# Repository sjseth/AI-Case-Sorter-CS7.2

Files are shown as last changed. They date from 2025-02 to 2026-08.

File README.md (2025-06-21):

# Welcome to the CS7.2 Case Sorter Project

This project is an adaptation and upgrade of the [CS7.1 Case Sorter](https://github.com/sjseth/AI-Case-Sorter-CS7.1) project and features a number of improvements as well as a dedicated electronics package. It doesn't replace the CS7.1 solution which will still be available for the foreseeable solution but instead provides an easier route to building the AI Case Sorter for those who don't want to mess around with all the wiring and soldering required in CS7.1. 

## Getting Started

### Step 1. Choose your parts option:

If you are interested in building this project, there are two main options you can choose from. 

<font style="color:gold">**Option #1:**</font> Buy the full build kit which includes all the non-3d printed parts needed for the assembly. Choose this option if you are starting from scratch and only want to build one machine. This will usually be the cheapest option in this case. The complete build kit is available here: [CS7.2 Complete Build Kit](https://shop.sjseth.com/products/cs7-2-complete-build-kit).  **Note you will still need to provide your own 12v 5amp powersupply and a computer to run the software.* 

<font style="color:gold">**Option #2:** </font>Buy the essentials kit which includes only those parts which can be sourced from SJSeth Solutions. If you choose this route, you will need to referr to the [CS7.2 Parts List](https://www.reloadingrecipes.com/Partslist/Display/1) and acquire all the parts necessary for the build. The essentials kit can be purchase here: [CS7.2 Essentials Kit](https://shop.sjseth.com/products/cs7-2-essentials-kit)

### Step 2. Print the parts needed for your build:

This repo contains all the stl files needed to complete your build. Those files are organized by assembly and available in the [Models](./Models/) folder. For your convenience these "EZ Build" zip files have been created which have only the models which are needed/required for this project. This is to say, you just need to print everything in the zip. Refer to the assembly guides for the recommended filaments and print settings. 

* [EZ Build For Complete Build Kit](./Full%20Parts%20Kit%20Build.zip)
* [EZ Build for Essentials Kit](./Essentials%20Build.zip)

### Step 3. Assemble The Sorter

Refer to the instructions in the [Instructions Folder](./instructions/) for each of the assemblies.

* [Camera](./Instructions/CS7.2%20Camera%20Assembly%20Guide.pdf) (not needed if buying full kit)
* [Homing Sensor](./Instructions/CS7.2%20Homing%20Sensor%20Assembly%20Guide.pdf) (not needed if buying full kit)
* [Classifier](./Instructions/CS7.2%20Classifier%20Assembly%20Guide.pdf)
* [Sorter](./Instructions/CS7.2%20Sorter%20Assembly%20Guide.pdf)
* [Electronics Enclosure](./Instructions/CS7.2%20Electronics%20Box%20Assembly.pdf)

### Step 4. Install the software and read the manual
You need to register for an account to download the software. You can do this at [https://www.reloadingrecipes.com/HeadstampSorter](https://www.reloadingrecipes.com/HeadstampSorter). 

Here is the link to the latest software manual: [AI Headstamp Sorter Application Guide for v1.1.53](./Instructions/AI%20Headstamp%20Sorter%20Application%20Guide_11531.pdf)

## CS7.2 Build Series Videos
### Camera Assembly
Camera Assembly (https://youtu.be/B2Un%2Dj%2DgyE4)

### Homing Sensor Assembly
Homing Sensor (https://youtu.be/8RCl6ofWERs)

### Classifier Assembly
Classifier Assembly (https://youtu.be/V4ZLb2sHJYE)

### Sorter Assembly
Sorter Assembly (https://youtu.be/yfZtguaGFcg)

### Electronics Box Assembly
Electroncis Box (https://youtu.be/7Ex8II1yqZ4)

### Final Assembly - putting it all together. 
Putting it all together (https://youtu.be/NzxutLAYxv8)

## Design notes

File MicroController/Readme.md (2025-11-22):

# CS7.2 Firmware

## Installing the firmware
1. Install Arduino Studio (https://www.arduino.cc/en/software/)
2. Download the latest firmware zip file from this folder (https://github.com/sjseth/AI-Case-Sorter-CS7.2/tree/main/MicroController)
3. Extract the zipfile and navigate into the folder and double-click on the CS72_Firmware.ino file to launch the file in the studio
4. In Arduino Studio, open the library panel (the icon on the left side which looks like books) and search for TMCStepper
5. Install the TMCStepper Library
6. Identify which COM port your board is plugged into. YOu can turn off the board and check the list of ports, then turn it back on. The new one that appears will be the com port for your board
7. Select the board/com port and set the board type as Arduino Uno
8. Push/Upload the firmware to the boards.  This is the button in the top left of the studio which looks like an arrow.

# Video Instructions

Updating Firmware On Board (https://youtu.be/qdWw8pG_hVo)

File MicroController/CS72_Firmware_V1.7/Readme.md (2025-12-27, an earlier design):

# V1.7 Firmware

## Important! This firmware is for v1.7 boards and newer. Right now, all the v1.7 boards are yellow... If your board isn't yellow, this won't work for you!

The board versions can be found in the lower left corner of the PCB. 

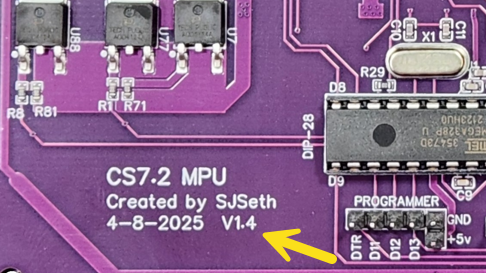
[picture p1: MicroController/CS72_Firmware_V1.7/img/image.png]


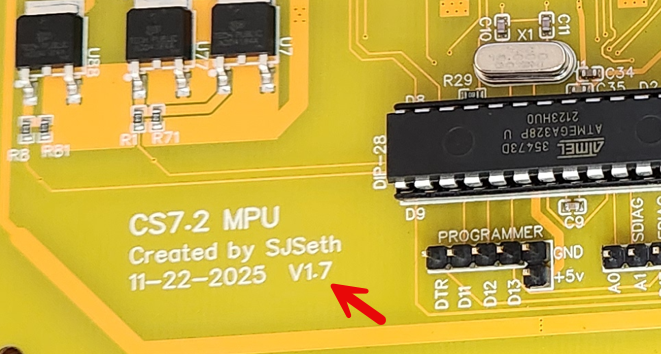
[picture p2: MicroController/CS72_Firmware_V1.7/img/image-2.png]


# FAQ

Q: What can this firmware do that the previous versions can't?

A: The v1.7+ boards have the TMC2209 diag pins wired up so that we can use the stallguard feature which allows us to monitor the current/resistance on the motor to detect a stall/jam.

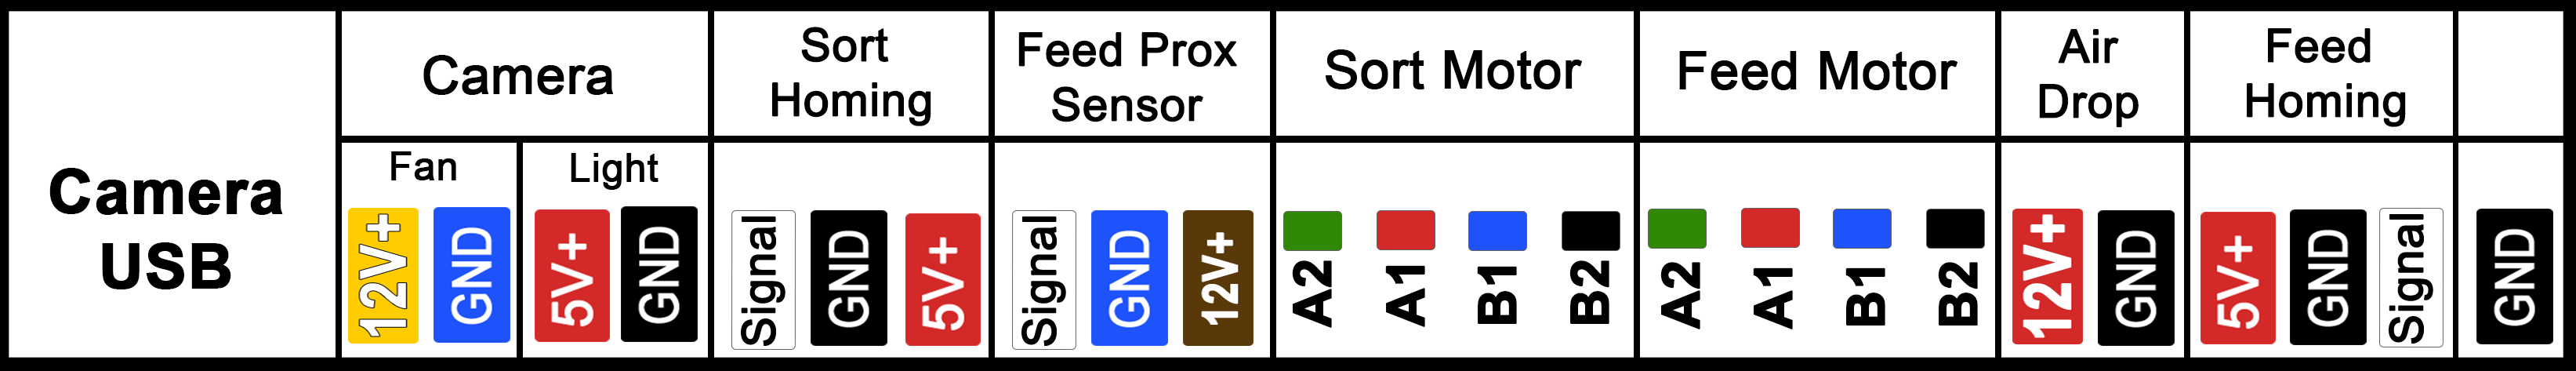
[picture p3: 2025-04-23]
Models/Electronics Enclosure/box_label_v3.png

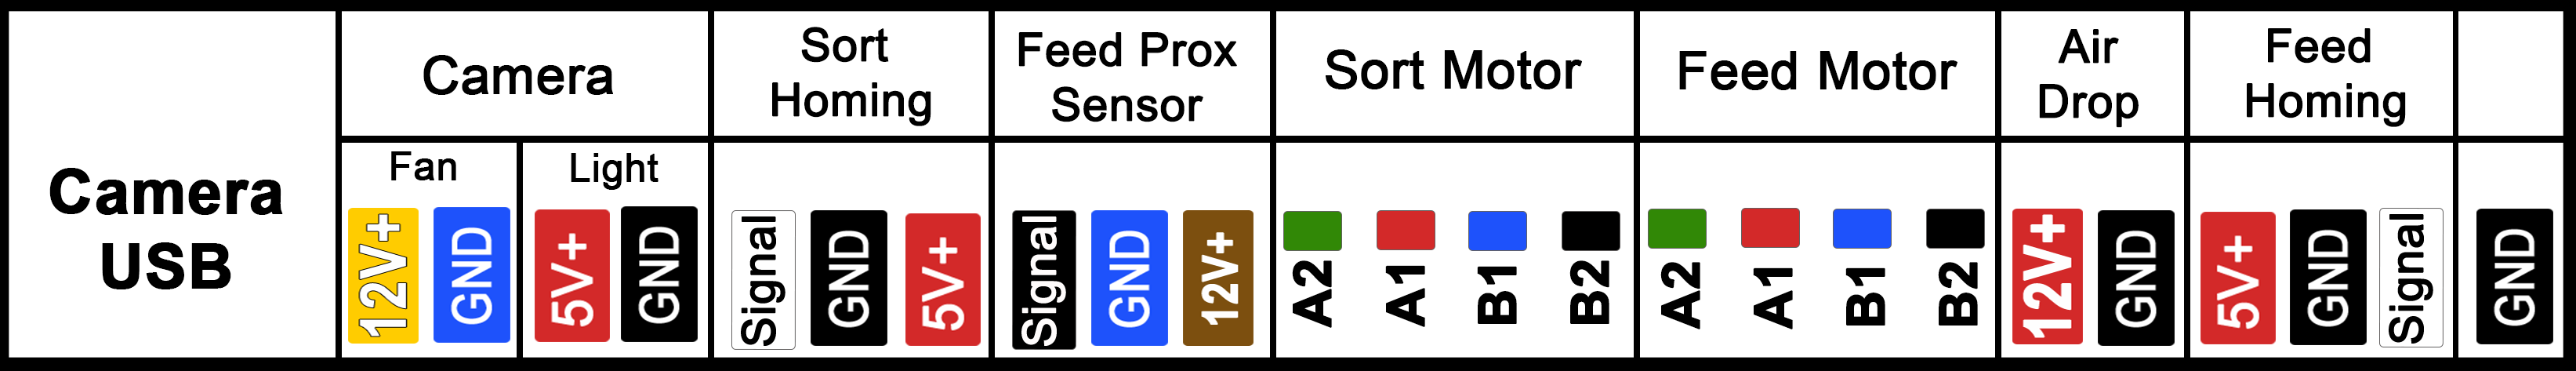
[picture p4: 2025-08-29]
Models/Electronics Enclosure/box_label_new.png

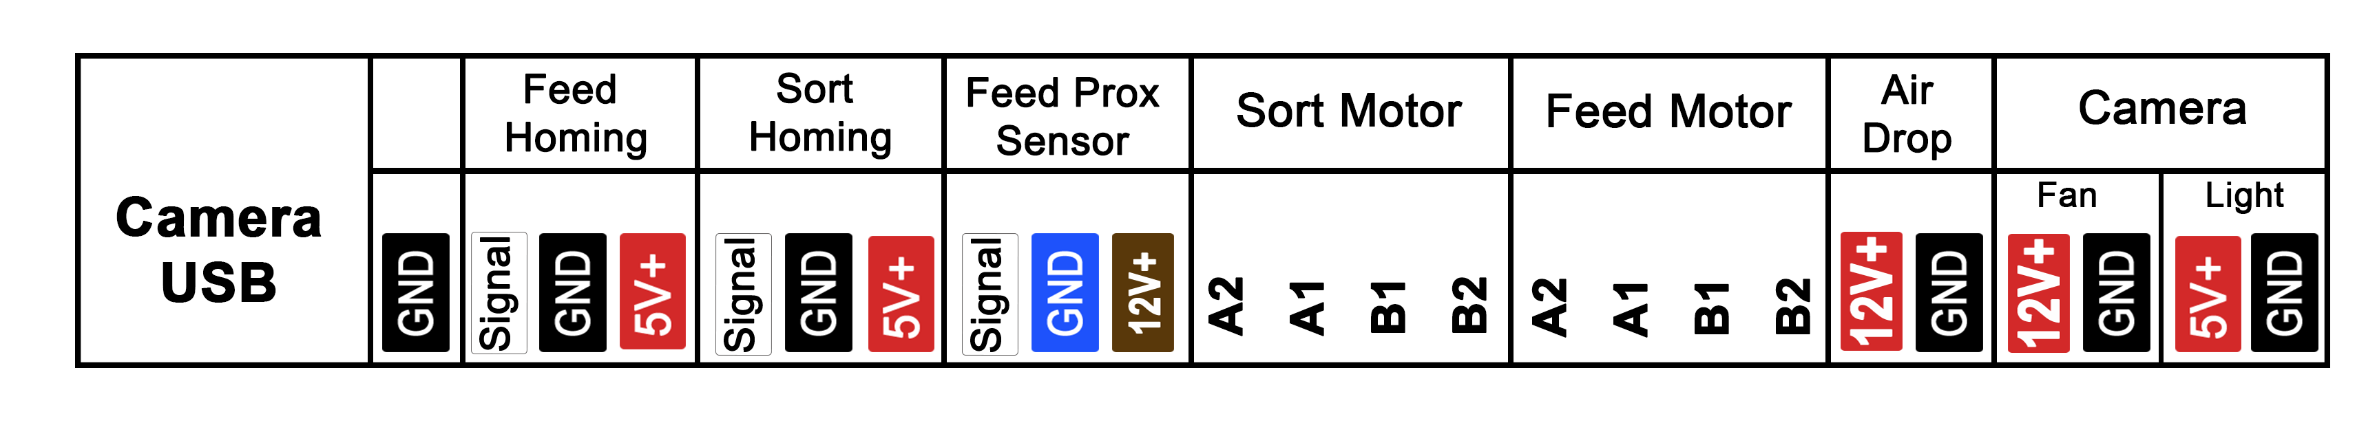
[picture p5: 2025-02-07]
Models/Electronics Enclosure/v1-v2/box_label_V2.png

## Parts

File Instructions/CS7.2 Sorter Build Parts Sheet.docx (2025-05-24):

(5) M3x8 Socket Head Cap Screw (2) Homing Sensor (1) Bracket Lock (2) Sort Pipe Set Screws | (4) M3x14 Phillips Pan Head Screw Motor Mount | (4) M3 Washers Motor Mount | (4) M3x12 Phillips Pan Head Screw Flange Motor Mount Screws
(1) 5mm Motor Flange with lock screws Motor Flange Coupler | (1) M3x18 Socket Head Cap Screws Homing Interrupter

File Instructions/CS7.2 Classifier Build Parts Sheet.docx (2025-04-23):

(1) M8x1.0 Heat Set Insert (for proximity sensor) Proximity Sensor | (1) M6x80 Socket Head Cap Screw Main Axle | (3) M6x30 Socket Head Cap Screws (1) Tension Cam Axle (2) Mount Screws | (1) M3x18 Socket Head Cap Screw Tension Cam Spring Mount
(1) M4x8 Socket Head Cap Screw Tension Cam Stop | (4) M3x12 Socket Head Cap Screws Motor Mount Screws | (2) M3x16 Socket Head Cap Screws Camera and Drop Tube Set Screws | (1) 5x5x30 Stainless Steel Tension Spring Tension Cam Spring
(1) M3 Nut (tension cam mount lock) Spring Mount Nut | (1) 5mm Motor Flange with lock screws Motor Flange Coupler | (4) M3x12 Phillips Pan Head Flange Gear Mount Screws | (2) 626zz Bearings Feed Wheel Bearings
(3) M3x8 Socket Head Cap Screws (2) Homing Sensor Mount (1) Light Shade Set Screw | (1) M3 Heat Set Insert Light Shade Lock | (1) .3x4x20mm Compression Spring Homing Sensor

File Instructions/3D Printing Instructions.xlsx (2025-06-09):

Part | Assembly | Quantity Required | Included in Full Kit | Filament Color | Recommended Filament Type | Layer Height | Infill | Walls | Support Type | Support Angle | Raft Layers | Github URL
Caliber Feed Wheels(all) | Classifier | 1 | No | Black | PLA+, PETG | 0.2 | 25 | 3 | organic tree | 3 | 0 | https://github.com/sjseth/AI-Case-Sorter-CS7.2/tree/main/Models/CaliberFeedSets/
CS7.2 Camera Housing.stl | Camera | 1 | Yes | Black | PLA+, PETG | 0.16 | 15 | 2 | none |  | 0 | https://github.com/sjseth/AI-Case-Sorter-CS7.2/tree/main/Models/Camera/CS7.2 Camera Housing.stl
CS7.2 Camera Light Diffuser.stl | Camera | 1 | Yes | White (non opaque) | PLA, PLA+ | 0.16 | 0 | 2 | none |  | 0 | https://github.com/sjseth/AI-Case-Sorter-CS7.2/tree/main/Models/Camera/CS7.2 Camera Light Diffuser.stl
CS72 - Camera Focus Jig.stl | Camera | 1 | No | Black | PLA+, PETG | 0.2 | 20 | 3 | none |  | 0 | https://github.com/sjseth/AI-Case-Sorter-CS7.2/tree/main/Models/Camera/CS72 - Camera Focus Jig.stl
CS7.2 Classifier Base.stl | Classifier | 1 | No | Black | PLA+, PETG | 0.2 | 20 | 3 | none |  | 0 | https://github.com/sjseth/AI-Case-Sorter-CS7.2/tree/main/Models/Classifier/CS7.2 Classifier Base.stl
CS7.2 Classifier Drop Nozzle.stl | Classifier | 1 | No | Any | PLA+, PETG | 0.2 | 20 | 3 | organic tree | 3 | 0 | https://github.com/sjseth/AI-Case-Sorter-CS7.2/tree/main/Models/Classifier/CS7.2 Classifier Drop Nozzle.stl
CS7.2 Drive Gear.stl | Classifier | 1 | No | Any | PLA+, PETG | 0.2 | 20 | 3 | none |  | 0 | https://github.com/sjseth/AI-Case-Sorter-CS7.2/tree/main/Models/Classifier/CS7.2 Drive Gear.stl
CS7.2 Feed Bracket.stl | Feed | 1 | No | Any | PLA+, PETG | 0.2 | 20 | 3 | organic tree | 3 | 0 | https://github.com/sjseth/AI-Case-Sorter-CS7.2/tree/main/Models/Classifier/CS7.2 Feed Bracket.stl
CS7.2 Homing Sensor.stl | Classifier | 1 | Yes | Any | PLA+, PETG | 0.16 | 20 | 3 | none |  | 0 | https://github.com/sjseth/AI-Case-Sorter-CS7.2/tree/main/Models/Classifier/CS7.2 Homing Sensor.stl
CS7.2 Tension Cam Shim.stl | Classifier | 1 | No | Any | PLA+, PETG | 0.2 | 20 | 3 | none |  | 1 | https://github.com/sjseth/AI-Case-Sorter-CS7.2/tree/main/Models/Classifier/CS7.2 Tension Cam Shim.stl
CS7.2 Tension Cam.stl | Classifier | 1 | No | Any | PLA+, PETG | 0.2 | 20 | 3 | tree | 3 | 0 | https://github.com/sjseth/AI-Case-Sorter-CS7.2/tree/main/Models/Classifier/CS7.2 Tension Cam.stl
CS7.2 Wheel Lock - Light Shade.stl | Classifier | 1 | No | Any | PLA+ | 0.2 | 20 | 3 | none |  | 0 | https://github.com/sjseth/AI-Case-Sorter-CS7.2/tree/main/Models/Classifier/CS7.2 Wheel Lock - Light Shade.stl
CS7.2 Electronics Box Lid.stl | Electronics Enclosure | 1 | No | Any | PLA+ | 0.2 | 20 | 3 | none |  | 0 | https://github.com/sjseth/AI-Case-Sorter-CS7.2/tree/main/Models/Electronics Enclosure/CS7.2 Electronics Box Lid.stl
CS7.2 Electronics Box.stl | Electronics Enclosure | 1 | No | Any | PLA+ | 0.2 | 20 | 3 | organic tree | 3 | 0 | https://github.com/sjseth/AI-Case-Sorter-CS7.2/tree/main/Models/Electronics Enclosure/CS7.2 Electronics Box.stl
CS7.2 Mount with Rotator - Plate.stl | Electronics Enclosure | 1 | No | Any | PLA+, PETG | 0.2 | 20 | 3 | none |  | 0 | https://github.com/sjseth/AI-Case-Sorter-CS7.2/tree/main/Models/Electronics Enclosure/CS7.2 Mount with Rotator - Plate.stl
CS7.2 Mount with Rotator.stl | Electronics Enclosure | 1 | No | Any | PLA+, PETG | 0.2 | 20 | 3 | none |  | 0 | https://github.com/sjseth/AI-Case-Sorter-CS7.2/tree/main/Models/Electronics Enclosure/CS7.2 Mount with Rotator.stl
CS7.2 Wire Cover.stl | Electronics Enclosure | 1 | No | Any | PLA+, PETG | 0.2 | 20 | 3 | none |  | 0 | https://github.com/sjseth/AI-Case-Sorter-CS7.2/tree/main/Models/Electronics Enclosure/CS7.2 Wire Cover.stl
CS7.2 Thumbscrew Cap.stl | Misc | (optional) 5 | No | Any | PLA+, PETG | 0.2 | 20 | 3 | none |  | 0 | https://github.com/sjseth/AI-Case-Sorter-CS7.2/tree/main/Models/Misc/CS7.2 Thumbscrew Cap.stl
CS7.2 Pole Mount - 1.050 with Channel.stl | Mounts | 3 | No | Any | PLA+, PETG | 0.2 | 25 | 3 | none |  | 0 | https://github.com/sjseth/AI-Case-Sorter-CS7.2/tree/main/Models/Mounts/CS7.2 Pole Mount - 1.050 with Channel.stl
CS7.2 Pole Mount - 1.050.stl | Mounts | (optional) 1 | No | Any | PLA+, PETG | 0.2 | 25 | 3 | none |  | 0 | https://github.com/sjseth/AI-Case-Sorter-CS7.2/tree/main/Models/Mounts/CS7.2 Pole Mount - 1.050.stl
CS7.2 Wire Mgmt Clip.stl | Mounts | (optional) 4 | No | Any | PLA+ | 0.2 | 20 | 3 | none |  | 1 | https://github.com/sjseth/AI-Case-Sorter-CS7.2/tree/main/Models/Mounts/CS7.2 Wire Mgmt Clip.stl
CS7.2 Pipe Bracket.stl | Sorter | 1 | No | Any | PLA+, PETG | 0.2 | 20 | 3 | none |  | 0 | https://github.com/sjseth/AI-Case-Sorter-CS7.2/tree/main/Models/Sorter/CS7.2 Pipe Bracket.stl
CS7.2 Sort Pipe - 40mm LO.stl | Sorter | 1 | No | Any | PLA+, PETG | 0.2 | 15 | 2 | none |  | 0 | https://github.com/sjseth/AI-Case-Sorter-CS7.2/tree/main/Models/Sorter/CS7.2 Sort Pipe - 40mm LO.stl
CS7.2 Sorter Base.stl | Sorter | 1 | No | Any | PLA+, PETG | 0.2 | 20 | 3 | none |  | 0 | https://github.com/sjseth/AI-Case-Sorter-CS7.2/tree/main/Models/Sorter/CS7.2 Sorter Base.stl
CS7.2 Sorter Homing Interupt.stl | Sorter | 1 | No | Black | PLA+, PETG | 0.2 | 20 | 3 | none |  | 0 | https://github.com/sjseth/AI-Case-Sorter-CS7.2/tree/main/Models/Sorter/CS7.2 Sorter Homing Interupt.stl

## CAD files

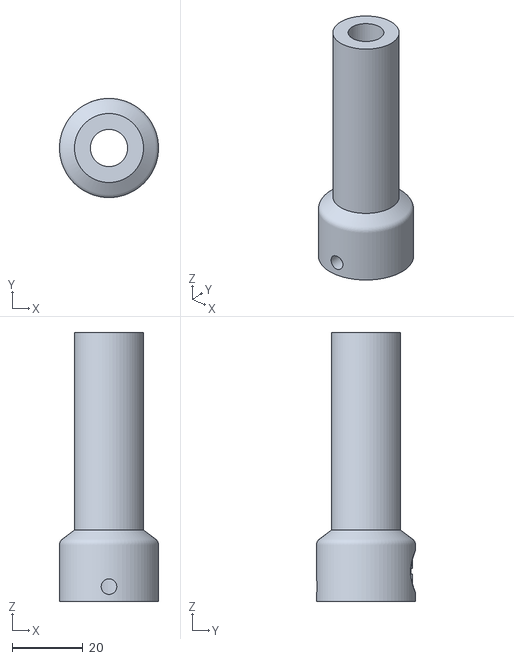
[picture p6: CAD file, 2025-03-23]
Models/CaliberFeedSets/223_556/CS7.2 Feed Tube - 223_556 (S).stl
28.0 x 28.0 x 76.0

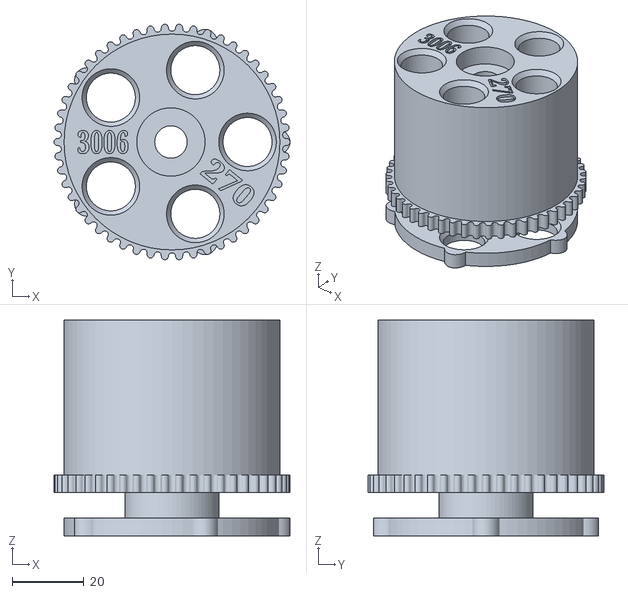
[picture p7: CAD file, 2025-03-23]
Models/CaliberFeedSets/30-06_270/CS7.2 Feed Wheel - 30.06 - (S).stl
65.6 x 65.5 x 60.0

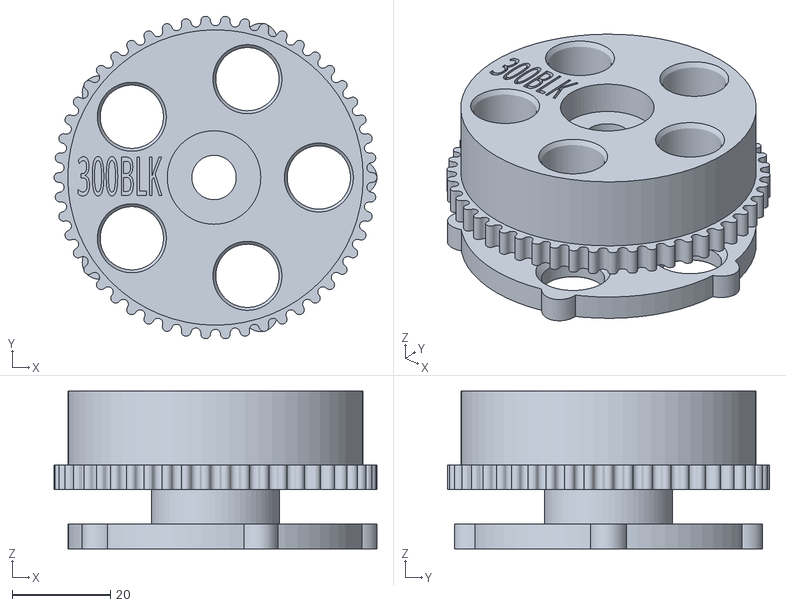
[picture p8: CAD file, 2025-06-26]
Models/CaliberFeedSets/300_Blackout/CS7.2 300 Blackout Feed Wheel.stl
65.6 x 65.5 x 32.0

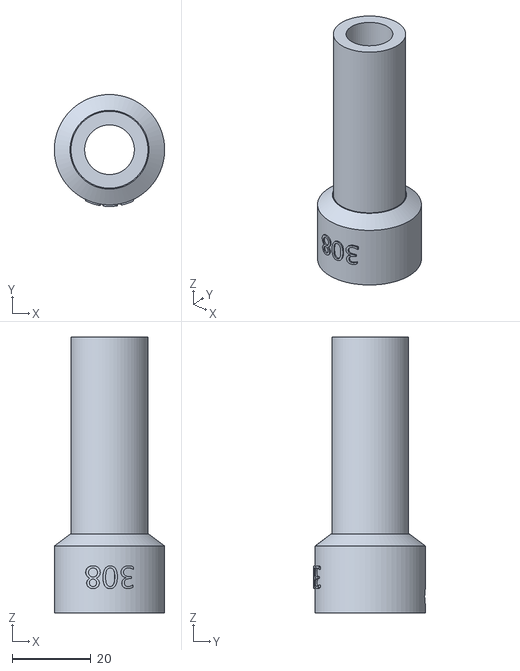
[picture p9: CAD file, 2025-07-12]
Models/CaliberFeedSets/308win/CS7.x 308Win Feed Nozzle.stl.stl
28.0 x 28.4 x 70.0

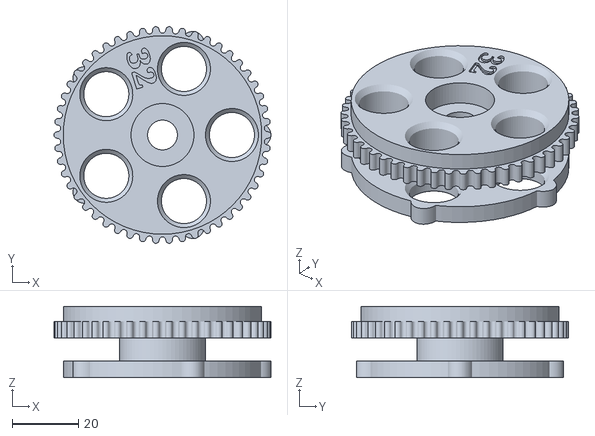
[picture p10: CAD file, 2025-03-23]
Models/CaliberFeedSets/32SWLong/CS7.2 Feed Wheel - 32SWLong - (S).stl
65.6 x 65.5 x 21.6

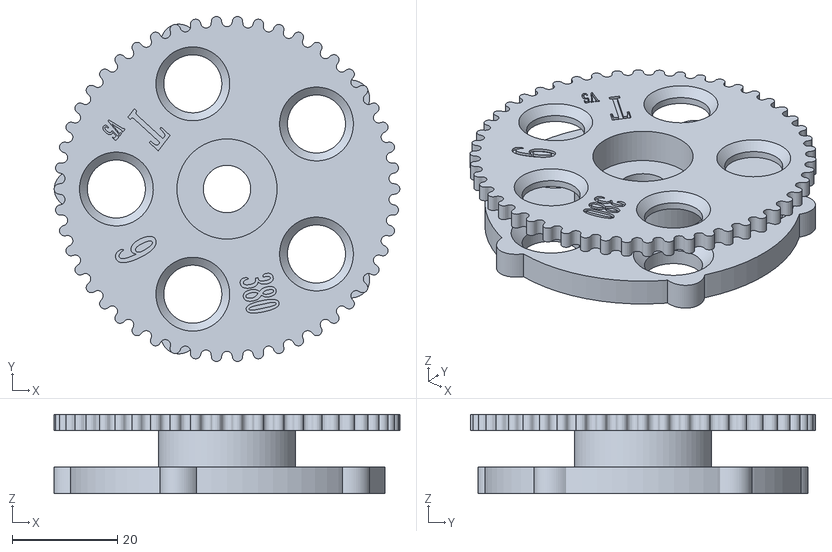
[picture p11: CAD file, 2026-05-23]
Models/CaliberFeedSets/380-9mm/CS7.x 9mm 380 Feed Wheel - Tight v5.stl
65.6 x 65.5 x 15.0

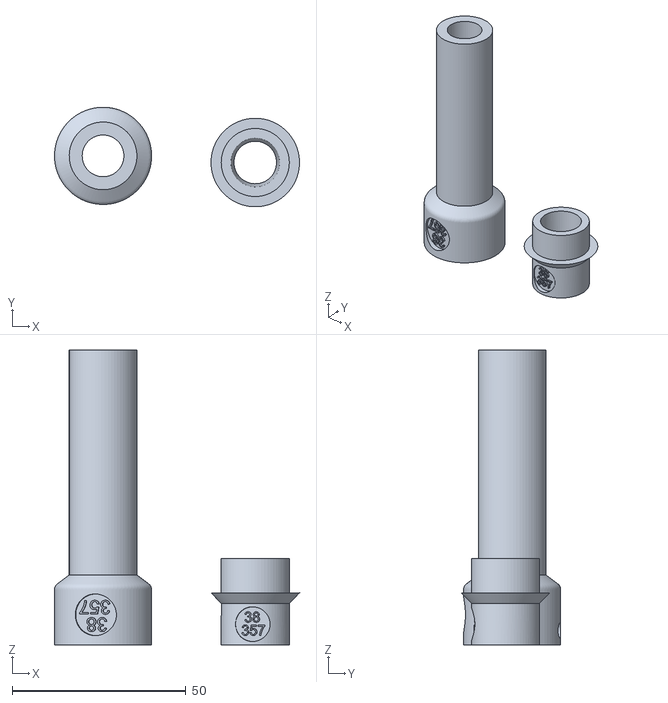
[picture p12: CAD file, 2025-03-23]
Models/CaliberFeedSets/38_Special/CS7.2 Feed Nozzle - 38Special - (S).stl
70.6 x 28.7 x 85.0

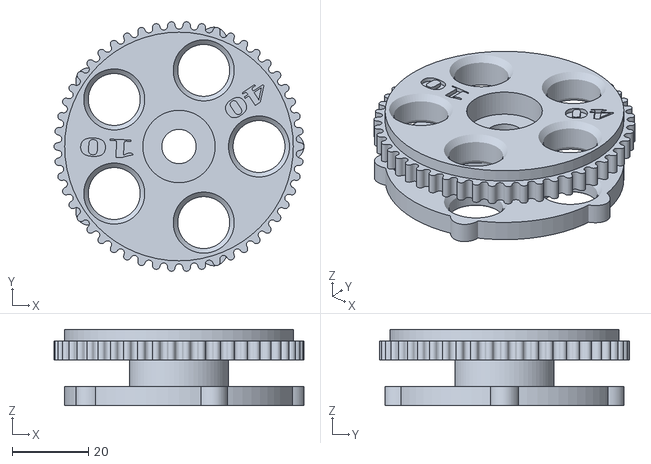
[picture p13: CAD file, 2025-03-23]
Models/CaliberFeedSets/40SW/CS7.2 Feed Wheel - 40SW (S).stl
65.6 x 65.5 x 20.0

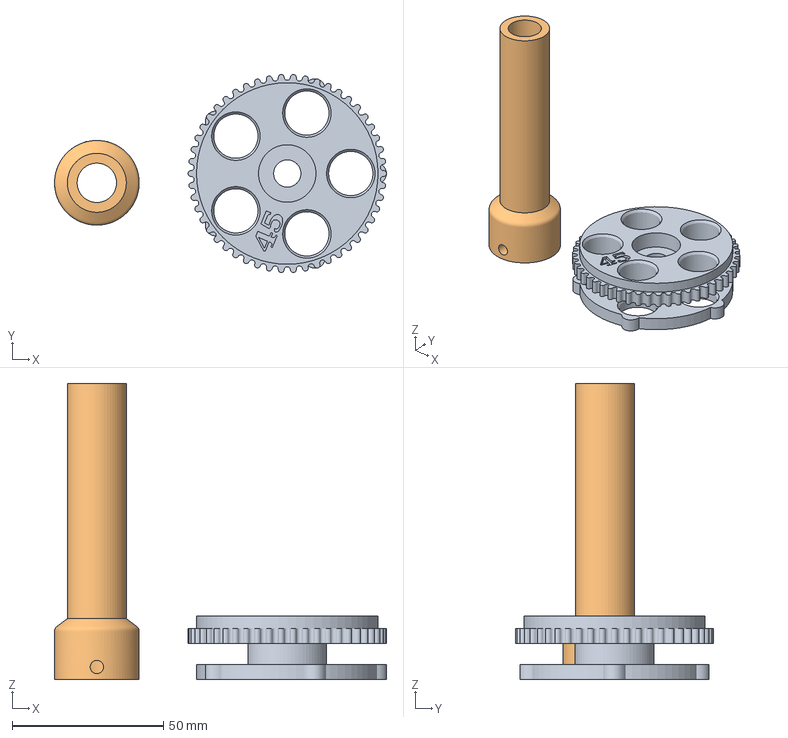
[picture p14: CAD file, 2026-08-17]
Models/CaliberFeedSets/45Auto/CS7.2 Feed Wheel 45AUTO (S).3mf
109.8 x 65.5 x 98.0 mm
CS7.2 Feed Wheel 45AUTO (S).stl
CS7.2 Feed Nozzle 45AUTO-GAP (S).stl_1

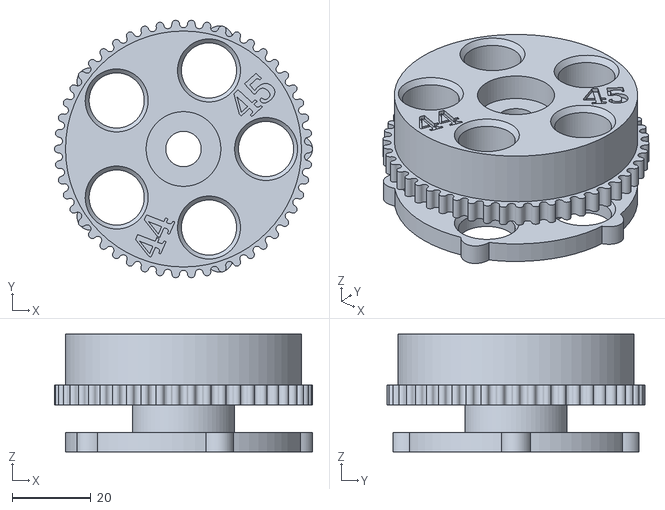
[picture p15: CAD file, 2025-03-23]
Models/CaliberFeedSets/45Colt_44Mag/CS7.2 Feed Wheel - 44MAG_45COLT (S).stl
65.6 x 65.5 x 30.0

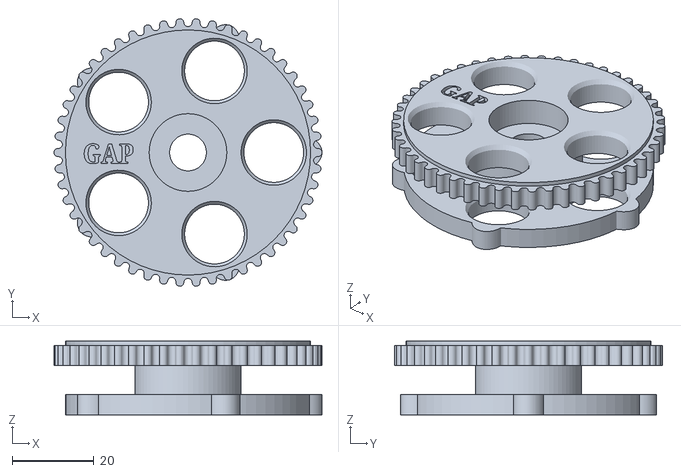
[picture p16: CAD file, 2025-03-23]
Models/CaliberFeedSets/45GAP/CS7.2 Feed Wheel - 45GAP - (S).stl
65.6 x 65.5 x 18.0

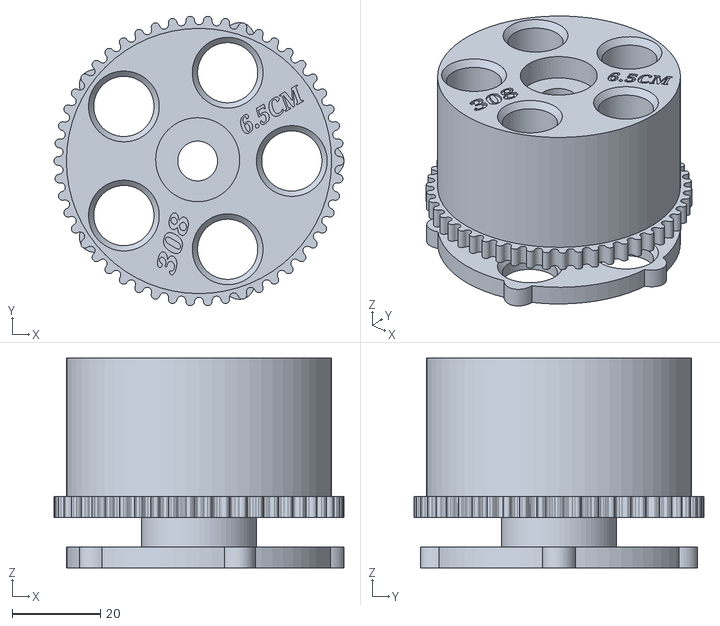
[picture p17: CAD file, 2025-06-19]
Models/CaliberFeedSets/6.5_Creedmoor/CS7.2 Feed Wheel - 6.5 Creedmoor (S).stl
65.6 x 65.5 x 47.5

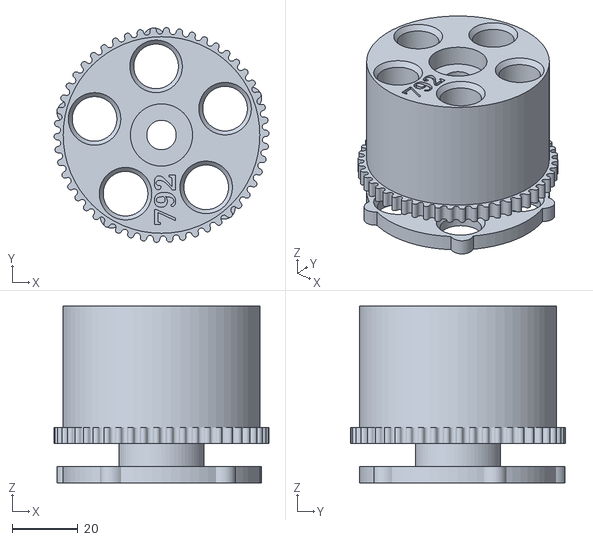
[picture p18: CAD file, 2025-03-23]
Models/CaliberFeedSets/7.92x57_Mauser/CS7.2 Feed Wheel - 7.92x57M - (S).stl
65.6 x 65.6 x 54.0

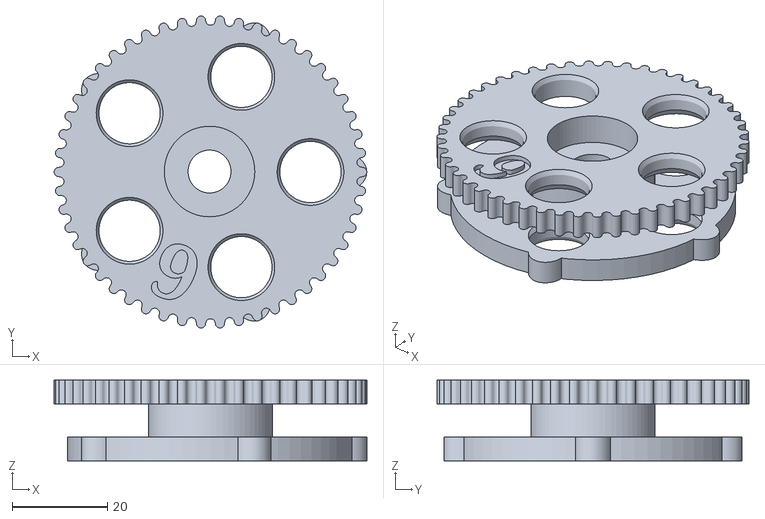
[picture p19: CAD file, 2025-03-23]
Models/CaliberFeedSets/9mm/CS7.2 Feed Wheel 9mm (S).stl
65.6 x 65.5 x 17.0

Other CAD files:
Models/CaliberFeedSets/CSxDrop_Nozzles/CS7.x 38 Special Drop Nozzle.stl
Models/CaliberFeedSets/CSxFeed_Tubes/CS7.x 30.06 Feed Tube.stl
Models/Camera/4010 Blower Fan Tuyere - Air Guide.stl
Models/Classifier/CS7.2 Homing Sensor V2.3mf
Models/CaliberFeedSets/223_556/CS7.2 Feed Tube - 223_556.stl
Models/CaliberFeedSets/223_556/CS7.2 Feed Wheel - 223_556 (S).stl
Models/CaliberFeedSets/30-06_270/CS7.2 Feed Nozzle - 30.06 - (S).stl
Models/CaliberFeedSets/300_Blackout/CS7.2 300 Blackout Feed Nozzle.stl
Models/CaliberFeedSets/308win/CS7.2 Feed Nozzle - 308 (S).stl
Models/CaliberFeedSets/308win/CS7.2 Feed Wheel - 308 (S).stl
Models/CaliberFeedSets/32SWLong/CS7.2 Feed Nozzle - 32SWLong - (S).stl
Models/CaliberFeedSets/380-9mm/CS7.2 Feed Nozzle - 9mm - 380 (S).stl
Models/CaliberFeedSets/380-9mm/CS7.2 Feed Wheel - 9mm - 380 (S).stl
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

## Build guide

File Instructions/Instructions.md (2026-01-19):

# Welcome to the CS7.2 Case Sorter Project

This project is an adaptation of the [CS7.1 Case Sorter](https://github.com/sjseth/AI-Case-Sorter-CS7.1) project and features a number of improvements as well as a dedicated electronics package. It doesn't replace the CS7.1 solution which will still be available for the foreseeable solution but instead provides an easier route to building the AI Case Sorter for those who don't want to mess around with all the wiring and soldering required in CS7.1. 

## Getting Started

### Step 1. Choose your parts option:

If you are interested in building this project, there are two main options you can choose from. 

<font style="color:gold">**Option #1:**</font> Buy the full build kit which includes all the non-3d printed parts needed for the assembly. Choose this option if you are starting from scratch and only want to build one machine. This will usually be the cheapest option in this case. The complete build kit is available here: [CS7.2 Complete Build Kit](https://shop.sjseth.com/products/cs7-2-complete-build-kit).  **Note you will still need to provide your own 12v 5amp powersupply and a computer to run the software.* 

<font style="color:gold">**Option #2:** </font>Buy the essentials kit which includes only those parts which can be sourced from SJSeth Solutions. If you choose this route, you will need to referr to the [CS7.2 Parts List](https://www.reloadingrecipes.com/Partslist/Display/1) and acquire all the parts necessary for the build. The essentials kit can be purchase here: [CS7.2 Essentials Kit](https://shop.sjseth.com/products/cs7-2-essentials-kit)

### Step 2. Print the parts needed for your build:

This repo contains all the stl files needed to complete your build. Those files are organized by assembly and available in the [Models](../Models/) folder. For your convenience these "EZ Build" zip files have been created which have only the models which are needed/required for this project. This is to say, you just need to print everything in the zip. Refer to the assembly guides for the recommended filaments and print settings. 

* [EZ Build For Complete Build Kit](../Full%20Parts%20Kit%20Build.zip)
* [EZ Build for Essentials Kit](../Essentials%20Build.zip)

#### Step 2a. Reuse parts from your CS7.1 Build:

If you have a 7.1 build, these parts are reusable in 7.2
- Light Shade
- Feed Tubes
- Feed Bracket
- Feed Wheels (caliber sets)
- Drop Tube
- Tension Cam Shim
- Drive Gear
- Sorting Bins
- Pole Mount Brackets (though the new ones have wire management channels)

### Step 3. Assemble The Sorter

Refer to the instructions in the [Instructions Folder](./instructions/) for each of the assemblies.

* [Camera](./CS7.2%20Camera%20Assembly%20Guide.pdf) (not needed if buying full kit)
* [Homing Sensor](./CS7.2%20Homing%20Sensor%20Assembly%20Guide.pdf) (not needed if buying full kit)
* [Classifier](./CS7.2%20Classifier%20Assembly%20Guide.pdf)
* [Sorter](./CS7.2%20Sorter%20Assembly%20Guide.pdf)
* [Electronics Enclosure](./CS7.2%20Electronics%20Box%20Assembly.pdf)

## CS7.2 Build Series Videos

### Camera Assembly
Camera Assembly (https://youtu.be/B2Un%2Dj%2DgyE4)

### Homing Sensor Assembly
Homing Sensor (https://youtu.be/8RCl6ofWERs)

### Classifier Assembly
Classifier Assembly (https://youtu.be/V4ZLb2sHJYE)

### Sorter Assembly
Sorter Assembly (https://youtu.be/yfZtguaGFcg)

### Electronics Box Assembly
Electroncis Box (https://youtu.be/7Ex8II1yqZ4)

### Final Assembly - putting it all together. 
Putting it all together (https://youtu.be/NzxutLAYxv8)

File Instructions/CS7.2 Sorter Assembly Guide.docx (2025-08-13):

# CS7.2 Sorter Assembly Guide

# Printing the parts

The models for the 3d printed parts for the classifier base are available in the “Sorter” folder in the GitHub CS7.2 repo.

https://github.com/sjseth/AI-Case-Sorter-CS7.2/tree/main/Models/Sorter

From this folder, you need to print the following models.

- CS7.2 Pipe Bracket
- CS7.2 Sort Pipe – 40mm LO or CS7.2 Sort Pipe – 200mm LO
- CS7.2 Sorter Base
- CS7.2 Sorter Homing Interrupt

For these parts here are the basic recommendations:

Filament: PLA+ or PETG.

Color: These parts can be printed in any color you have available.

Layer Height: .2 or finer

Support: Recommend using tree support for the sorter base, however, use the support mode you get the best results with on your printer. For Bambu printers, I have found these settings work well:

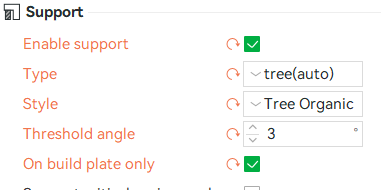
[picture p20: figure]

Note that other slices such as Cura, the support angle may read 87 degrees (opposite of Bambu/Orca slicer)

Strength/Density: 3 walls, 20% infill

# Assembly

Tools Required:

- Screwdriver with bits or Allen keys for M3, M6 socket head cap screws
- Small Phillips head screwdriver

Hardware required:

- (4) M3x14 Phillips Head Screws (motor mount)
- (4) M3 washers
- (4) M3x12 Phillips Head Screws (for flange mount)
- (3) M3x8 Socket Head Screw (set screw for base mount and sort pipe)
- (1) 5mm Motor Flange with lock screws
- (1) m3x18 Socket Head (clamp screw for homing interrupter)
- (optional) Small Zip Ties .1”W x 4”L

Electronics

- (1) Nema 17 Motor
- (1) Optical Homing Sensor

The following diagram is a quick reference to where the hardware belongs.

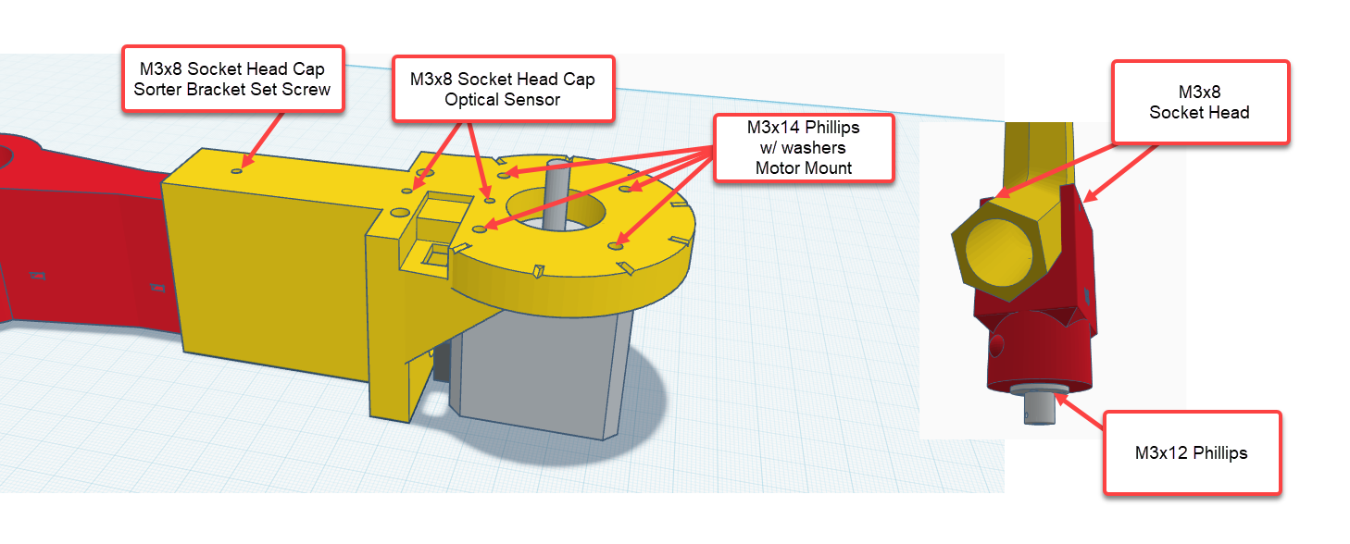
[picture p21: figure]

## Assembly Steps

1. Remove 3d printed support material from Sorter Base.
2. Run cable for sensor passing it through the inside of the sorter base, and up through the square hole

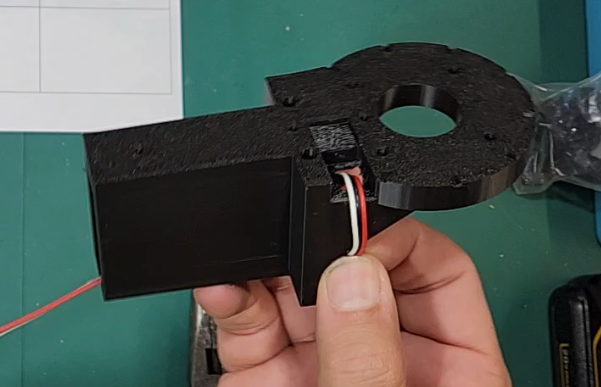
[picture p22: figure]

3. Install Optical Sensor using two M3x8 socket head screws and connect the cable. The clips on the connector should be face down. In the orientation for the picture above, the white wire is on the left, black on the right, red in the center.

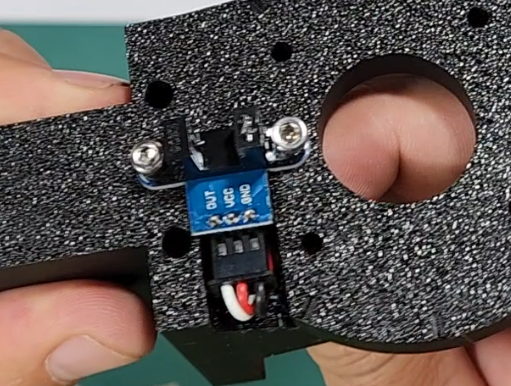
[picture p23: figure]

4. Run the motor cable through the inside of the sorter base and connect to the Nema 17 motor.
5. Attach the motor to the sorter base with the cable facing the wire management hole in the bracket.

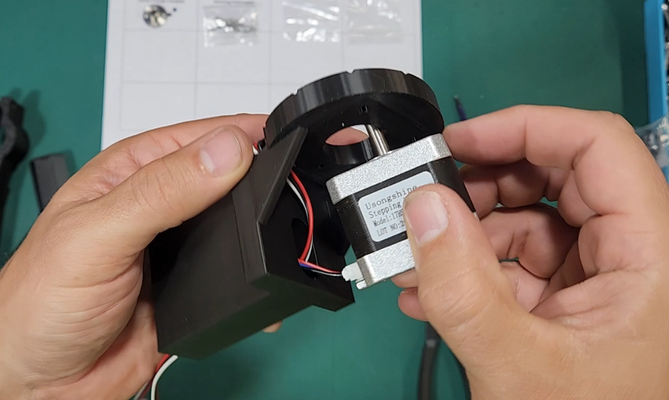
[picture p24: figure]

6. Attach the motor using 4 m3x14 Phillips screws and 4 washers. The washers are important here to prevent the motor from being pulled through if there is excessive heat buildup.

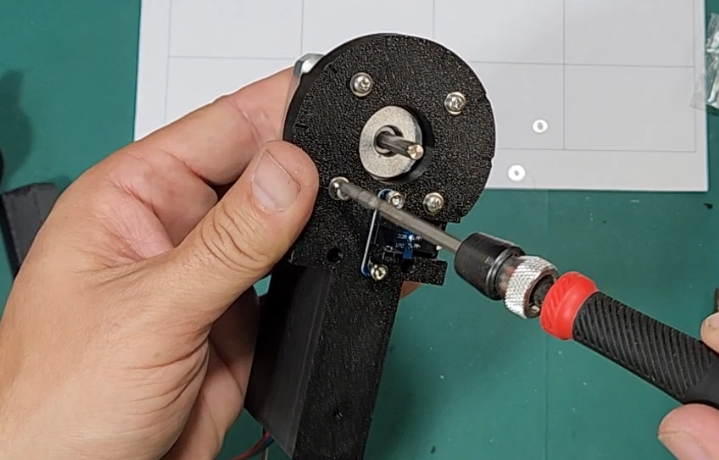
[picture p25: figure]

7. Install the 5mm Motor flange onto the bottom (recessed) side of the Sort Pipe Bracket. This should be installed using 4 of the Phillips head m3x12mm screws. The screws should go through the flange and thread into the bracket
8. Attach the homing sensor interrupt to the bottom of the sorter pipe bracket using one m3x18 screw. Tighten just enough so that the interrupter can still be rotated around the bracket

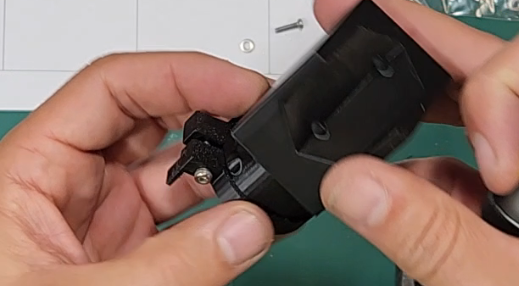
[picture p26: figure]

9. Add set screws to the flange and then slide it down over the motor shaft, locking the set screws in place. One of the set screws should lock down on the flat side of the motor shaft.
10. Clip the sorter tube into the sorter bracket ensuring that the two indexing slots are aligned.
11. Insert a m3x8 socket head screw into both sides of the sorter bracket to hold the pipe securely in place.
12. Rotate the Bracket/pipe until it is aligned with the 1st indexing notch on the sorter base.
13. Rotate the sort homing interrupt until it covers the first half of the sensor slot. Tighten down the interrupt lock screw.

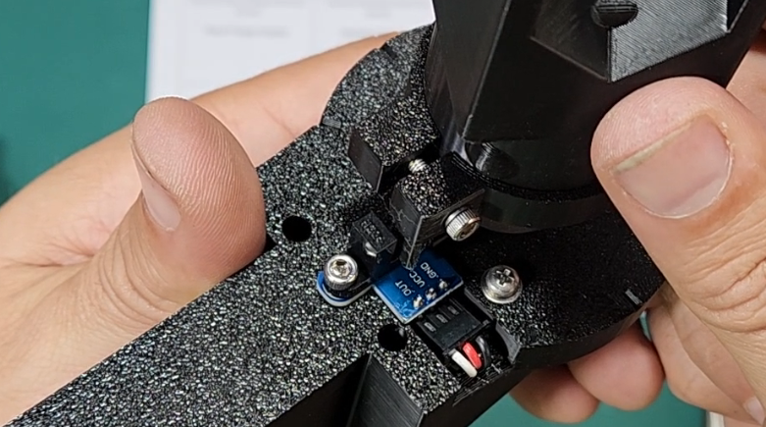
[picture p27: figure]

14. Insert the pole mount bracket into the sorter base ensuring that the motor and sensor wire are guided in the wire management channel in the bracket.
15. Use a m3x8 socket head screw as a set screw to keep the two pieces in place (do not over tighten as we will need to adjust this during the install and don’t want to create a dent yet in the bracket.

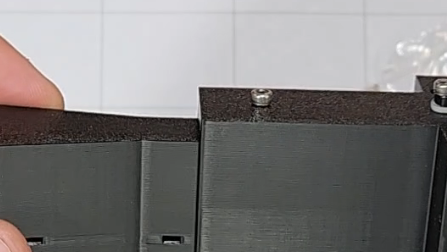
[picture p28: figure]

This completes the bottom half of the sorter build. It is now ready to be mounted to the pole and connect up to the electronics.

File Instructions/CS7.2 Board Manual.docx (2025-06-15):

# CS7.2 MPU - v1.4 User Guide

# Introduction

This board is designed to be used with the CS7.2 Case Sorter project located at (https://github.com/sjseth/AI-Case-Sorter-CS7.2).

## Key Features

- Integrated TMC2209 motor controllers
- USB Hub for single point connection to MPU and Camera
- Ultra clean 5v power supply with short circuit protection
- ATMEGA328P-U in DIP28 Socket for easy replacement/repair
- Integrated software dimmer for Camera Light
- Integrated MOSFET 12V relay for external air solenoid control
- Spring Clamp Terminals for easy install of wires and/or ferrules.
- Integrated power input and switch.

## Recommended Power Supply

The recommended power supply for this board is a 12V DC, 5amp power supply. The power supply needs to have a 5.5mm x 2.5mm tip positive jack.

# Description of Components

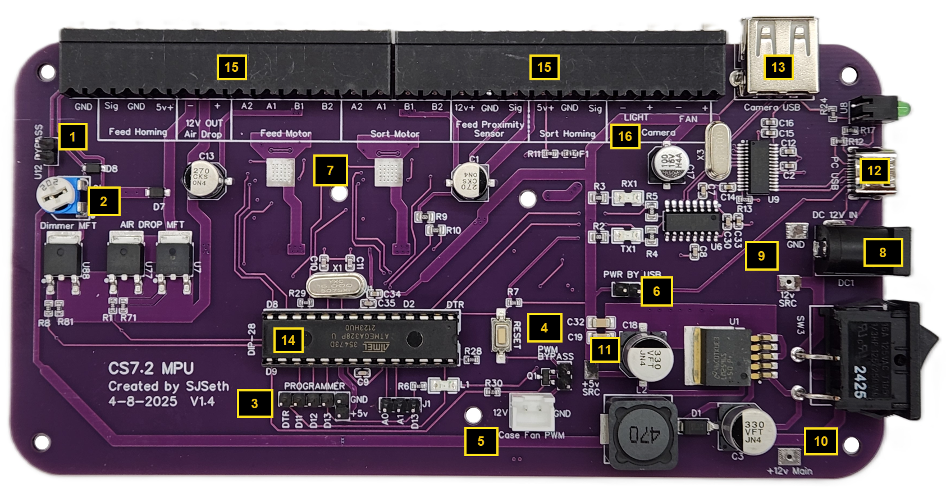
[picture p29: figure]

1. Light Control Variable Resister Bypass – In the event of a failure of the variable resistor or in the case that you want to send maximum power to the camera lighting; you can place a jumper on these pins to bypass the resistor completely.

2. Light Control Variable Resister (2kohm) – The variable resistor should be preset when shipped but can be adjusted to provide additional dimming (counterclockwise) if necessary.

3. Programmer for bootloader – These pins are used to install the bootloader on the ATMEGA32PU chip. This is completed before the boards are shipped and should not be used unless you need to replace the ATMEGA32 chip.

4. Case Fan Speed PWM Bypass – The firmware for CS7.2 has an option to set the case fan speed. By default, it is set to 100%. If you want to bypass the case fan dimmer for max power, place a jumper on these pins.

5. Case Fan Connector – This is a 12V connector designed to be used with your case fan cooling solution and labels for both 12v and GND are found on either side of the connector to indicate the polarity.

6. PWR by USB jumper – Allows board to be powered by computers 5V over USB. Though it is not recommended to be set during normal use, it can be used if you want to program the board without connecting it to an external power supply.

7. Ground Pads for motor Heat Sinks – The boards typically come with the heat sinks preinstalled. The Trinamic TMC2209 Motor Controllers are located on the bottom side of the board and have ground pads with vias to help transport heat to the top of the board.

8. 12v DC Barrel Connector – Accepts 5.5mm x 2.5mm, Tip Positive plug

9. Test Pads for 12v input – Test pads can be used with meter to ensure power supply is providing 12v in correct polarity.

10. 12v+ main (post switch) – Test pad can be used with meter to ensure power switch is working

11. 5v+ test pad – Test pad used to test 5v power supply.

12. USB-C connector – This connects to your computer.

13. USB-A connector – This connects to your camera.

14. DIP-28 Socket for ATMEGA32P-U – This socket allows you to replace the ATMEGA32P-U chip in case of failure.

15. Spring Terminal Clamp interface - The spring terminals provide an easy way to connect the various sensors and motors to the board.

16. Camera Light and Fan connectors – The [FAN+] is 12v+. The [LIGHT+] is a variable 5V+ Max connector. This is controlled by a combination of the variable resistor (#2) and the PWM via software (D11).

# Connecting Motors and UART Control

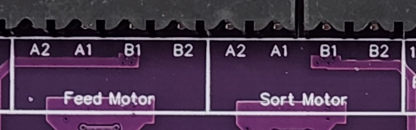
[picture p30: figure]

Important! – Be sure you have powered off the board before connecting or disconnecting motor wires. Failure to do this may result in a damaged motor controller which causes the board to be useless.

The motor controllers are labeled using the typical motor coil labels of A1, A2, B1 and B2 where A1 represents the positive side of the first coil and A2 is the negative side of the first coil. When connecting motors, it is important to ensure that the 1s and 2s are same polarity. If A1 is positive, B1 should also be positive.

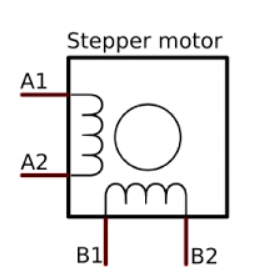
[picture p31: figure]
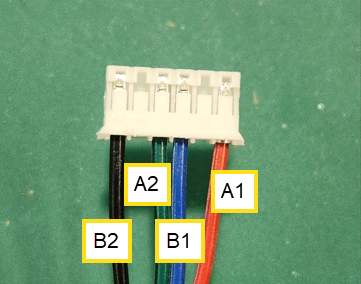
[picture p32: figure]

In a typical Nema17 pinout, the pins will be oriented as seen in the connector above. If your motors shake or stagger when starting, you will need power off the board and reconnect the pins to the correct terminals, so the coils are connected correctly. Here is a great video on the topic and covers how to verify your coils: https://www.youtube.com/watch?v=mPSPtvD8PiU

The CS7.2 Kit comes with the motor wires which already correspond to the colors on the labeling. If your motor wires connectors are wired differently than the image above, you cannot use the coloring on the kit labels unless you reposition the wires in the connector. Wires can be repositioned by slightly bending up the plastic clip on the connector and pulling the wire out.

# Microprocessor (MPU) Terminal Pin Map

ATMEGA32P-U Pin | Interface
1 (reset) | Reset Button
2 - D0 - (RX) | Connected to CH340
3 - D1 - (TX) | Connected to CH340
4 – D2 | Sort Motor Pulse
5 – D3 | Sort Motor DIR
6 – D4 | Sort Motor EN
11 – D5 | Sort Motor Driver (TMC2209) UART (RX)
12 – D6 | Sort Motor Driver (TMC2209) UART (TX)
13 – D7 | Feed Motor Pulse
14 – D8 | Feed Motor DIR
15 – D9 | Case Fan PWM
16 – D10 | ST - Feed Proximity Sensor - SIG
17 – D11 | Camera Light PWM
18 – D12 | Airdrop MFT
19 – D13 | D13 Pin, D13 LED
23 – A0 | Feed Motor EN, A0 Pin
24 – A1 | A1 Pin
25 – A2 | ST – Sort Homing Sensor - SIG
26 – A3 | ST - Feed Homing Sensor - SIG
27 – A4 | Feed Motor Driver (TMC2209) UART (RX)
28 – A5 | Feed Motor Driver (TMC2209) UART (TX)

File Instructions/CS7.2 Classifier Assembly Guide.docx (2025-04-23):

# CS7.2 Classifier Assembly Guide

# Printing the parts

The models for the 3d printed parts for the classifier base are available in the “Classifier” folder in the GitHub CS7.2 repo.

https://github.com/sjseth/AI-Case-Sorter-CS7.2/tree/main/Models/Classifier

From this folder, you need to print all models.

- CS7.2 Classifier Base
- CS7.2 Classifier Drop Nozzle
- CS7.2 Drive Gear
- CS7.2 Feed Bracket
- CS7.2 Homing Sensor
- CS7.2 Tension Cam Shim
- CS7.2 Tension Cam
- CS7.2 Wheel Lock – Light Shade

In addition, you need to print a caliber feed set for the caliber you wish to sort. The caliber feed sets are available in the CaliberFeedSets folder at:

https://github.com/sjseth/AI-Case-Sorter-CS7.2/tree/main/Models/CaliberFeedSets

From the caliber selected, (for example 9mm), there are two parts needed:

- CS7.2 Feed Nozzle 9mm
- CS7.2 Feed Wheel 9mm

For these parts here are the basic recommendations:

Filament: PLA+ or PETG.

Color: For some of the parts, the color effects the imaging quality. It is recommended to print the classifier base, feed wheel, tension cam and light shade in black. If you choose another color, be sure to paint or black out the bottom surfaces of these parts which are visible by the camera. The other parts can be any color which suits your tastes.

Layer Height: .2 or finer

Support: Recommend using tree support for entire project, however, use the support mode you get the best results with on your printer. For Bambu printers, I have found these settings work well:


Note that other slices such as Cura, the support angle may read 87 degrees (opposite of Bambu/Orca slicer)

Strength/Density: 3 walls, 20% infill

# Assembly

Important! Before starting the assembly of the classifier base, you need to first assemble the Camera module and the homing sensor module. Please refer to the Camera Module Assembly Guide and the Homing Sensor Guide for those assembly steps.

Once you have completed those assemblies, you can continue with the classifier assembly.

Tools Required:

- Screwdriver with bits or Allen keys for M3, M4,M6 socket head cap screws
- Soldering Iron or other heat source for installation of heat set insert

Hardware required:

- (1) Nema17 Motor
- (2) M3x16 Socket Head Cap Screws
- (4) M3x12 Socket Head Cap Screws
- (1) M3 Nut (tension cam mount lock)
- (1) M3x18 Socket Head Cap Screw
- (3) M3x8 Socket Head Cap Screws
- (4) M3x12 Phillips Head Screws (for drive gear)
- (1) M4x8 Socket Head Cap Screw
- (1) M6x80 Socket Head Cap Screw
- (1) M6x30 Socket Head Cap Screws
- (1) M8x1.0 Heat Set Insert (for proximity sensor)
- (1) M3 Heat Set Insert (for light shade)
- (1) .5x5x30 Stainless Steel Tension Spring
- (1) 5mm Motor Flange with lock screws
- (optional) Small Zip Ties .1”W x 4”L

Electronics

- (1) PNP-NO Proximity Sensor (LJ8A3-2-Z/BY)
- (1) Camera Module (see Camera Assembly Guide)
- (1) Nema 17 Motor
- (1) Optical Homing Sensor (see Homing Sensor Assembly guide)

The following diagram is a quick reference to where the hardware belongs.

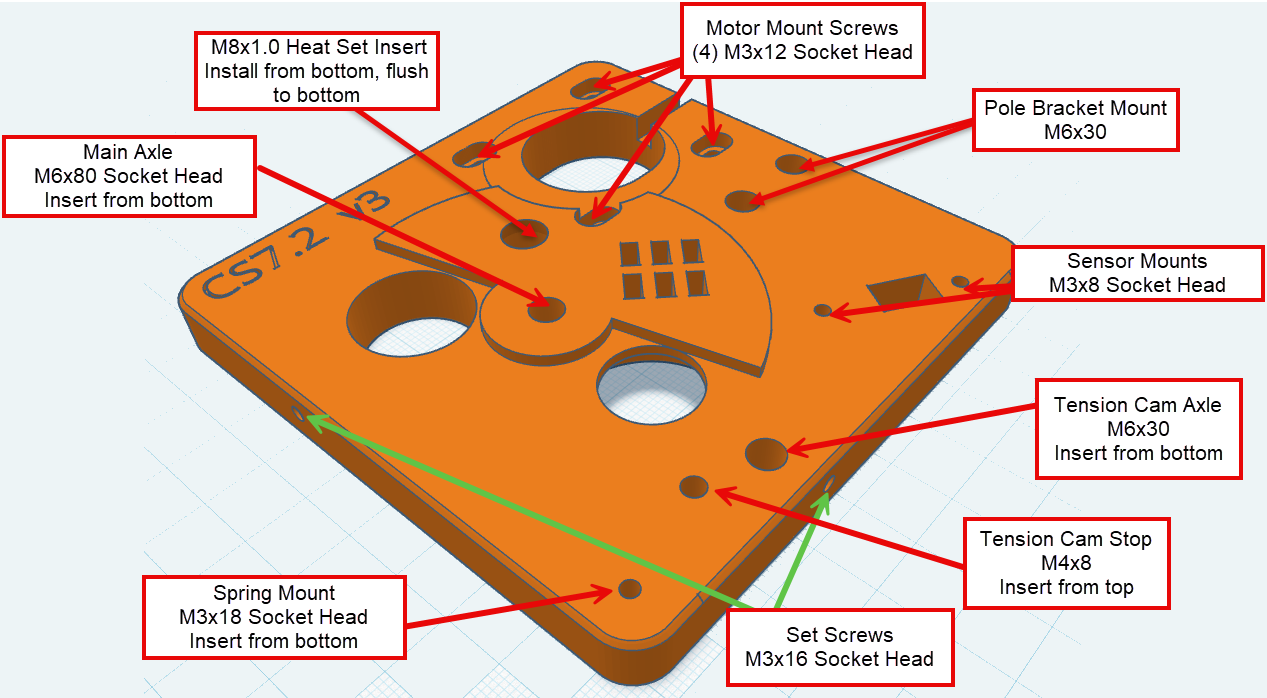
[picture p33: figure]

## Assembly Steps

1. Turn the classifier base upside down and remove the 3d printing supports from the camera hole.
2. Prepare your proximity sensor by removing the nuts and lock washers from it. Set it to the side in a convenient location as you will need to access quickly after the next step.
3. On the bottom of the classifier base, without using heat, press the narrow end (smooth end) of the M8 heat set insert into the appropriate hole (see diagram above). It should look like the following image:

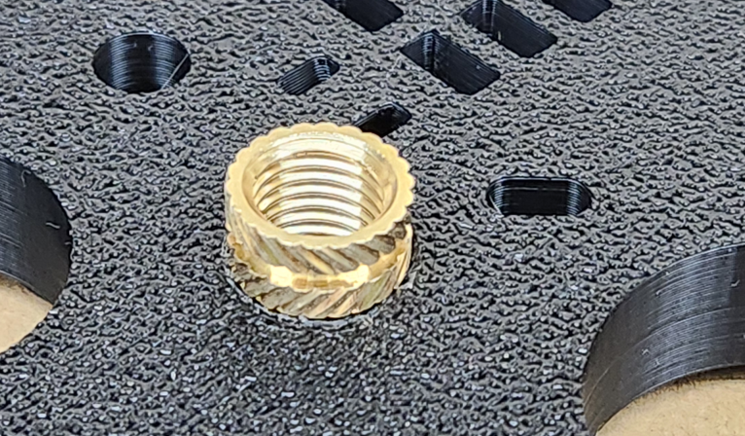
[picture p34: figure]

4. With the soldering iron on medium heat (if adjustable), push the soldering iron straight down in the center of the insert with light pressure. It should only take a few seconds before it begins to move and then use firm pressure to set it flush to the base. Do not overheat the nut or it will continue to melt through. Quickly remove the iron and thread the proximity sensor in a few turns. The nut will still be hot and the plastic pliable so use this opportunity to align the sensor so that is perpendicular to the base. Hold it in place until the plastic cools down (usually 10 – 15 seconds). You can always reheat the nut if needed but just be careful not to overheat. As soon as the nut moves a little bit, remove the iron as there is a small delay as the heat radiates through the insert.
5. Remove the proximity sensor. (we will install it a bit later. )
6. Install the main axle M6x80 from the bottom. Be sure not to overtighten and just thread it until it stops. If using an electric driver, it is a good idea to use the clutch or go slow so you don’t strip the plastic.
7. Install the cam shaft axle (M6x30) from the bottom. Same procedure as above to prevent stripping.
8. Install the spring mount (M3x18) from the bottom.
9. Install the Tension Cam Stop screw (M4x8 Socket Head Cap Screw) from the top threaded all the way down to the base but DO NOT OVERTIGHTEN.
10. Install the proximity sensor. Take one nut and thread it back on the sensor, thread the sensor into the insert until the top of the sensor is flush with the top of the base. It should not protrude above the base as it will interfere with the feed wheel.
11. Install the motor with the 4 m3x12 socket head screws. Position it so that it is pushed all the way back near the closest edge of the base. Tighten these screws until snug but DO NOT OVERTIGHTEN.
12. Install the camera and drop tube set screws (m3x16 socket head) so that they are flush with the holes they are setting for. Use a finger to feel for the screw as you thread it in and then back it out a little.
13. Install the camera so that the fan is facing away from the pole bracket mount. The camera has notches on the top which align with the existing two m6 axle screws. Once the camera is pressed firmly in place, tighten the set screw slowly until it locks the camera in place. DO NOT OVERTIGHTEN.
14. Install the drop nozzle and tighten set screw until it contacts the nozzle. DO NOT OVERTIGHTEN.
15. Install the homing sensor, the sensor should be positioned as far back (away from the center) as possible. We can move it forward later if not making good contact.
16. Install the Tension Cam shim. This should thread on easily by hand and sit flush to the base. If it is too loose or tight, you can quickly reprint this part and use the slicer to scale it up or down by 1%.
17. Remove any 3d printing support from the bottom of the tension cam and then attach one end of the extension spring to the knob on the tension cam. It may be necessary to use needle nose pliers to bend the loop on the spring out a little, so it fits over the knob.
18. Slide the tension cam over the axle and shim and attach the spring to the spring mount screw. Add an m3 nut to the top
19. Install the 5mm Motor flange onto the bottom (recessed) side of the Drive Gear. This should be installed using 4 of the Phillips head m3x12mm screws. The screws should go through the flange and thread into the gear.
20. Add set screws to the flange and then slide it down over the motor shaft, locking the set screws in place. One of the set screws should lock down on the flat side of the motor shaft.
21. Add two bearings to your caliber set feed wheel. The bearings are press fit but should pop into place with a bit of pressure.
22. Slide the caliber feed wheel down over the axle while pulling the tension cam out to let the wheel fully seat. The tension cam should snap back into place holding the wheel. You may need to twist or adjust the wheel to mesh with the drive gear.
23. Next we need to assemble the light shade. This requires the installation of an m3 heat set insert. The same procedure applies as was used for the larger m8 insert but since the main body of the light shade assembly is round, it is recommended to secure it lightly in a vice or clamp. Also it is recommended to put an extra M6 screw through center of the light shade body to prevent inserting the insert too far. Using heat, press in the insert. If it is contacting the m6 screw so that the screw cannot be removed, it is in too far, you can heat the insert a little and use the screw to push it flush to the inside of the hole. After you have installed the insert and let it cool down (this is important), thread an m3x8 socket head screw through the insert to ensure it can lock down on the m6 axle.
24. Now the light shade and the light shade body can be press fit or snapped together. It should look like the following diagram if done correctly:

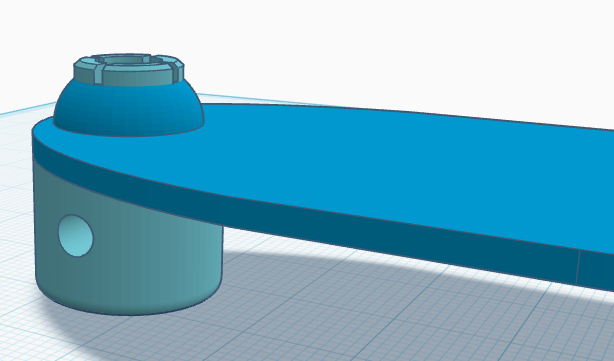
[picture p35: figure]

25. Finally, we can install the shade and lock on the main axle. The narrow side (snap lock side) should face down and contact the bearing of the feed wheel.

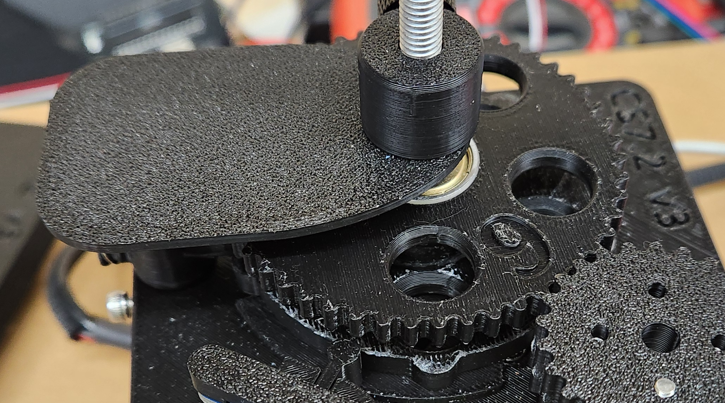
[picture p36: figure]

26. Install the mount bracket to the classifier base using two M6x30 socket head screws.
27. Attach your homing sensor cable by sliding it up through the square hold provided and connecting it to the sensor
28. Now is the time for cable management. You can use the zip tie mount points on the bottom of the classifier base if needed or just organize the cables so they are cleaning passing through the channel in the base of the mounting bracket. See the following example:

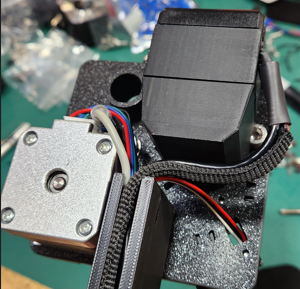
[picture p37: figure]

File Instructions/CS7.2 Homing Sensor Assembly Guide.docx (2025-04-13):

# CS7.2 Homing Sensor Assembly Guide

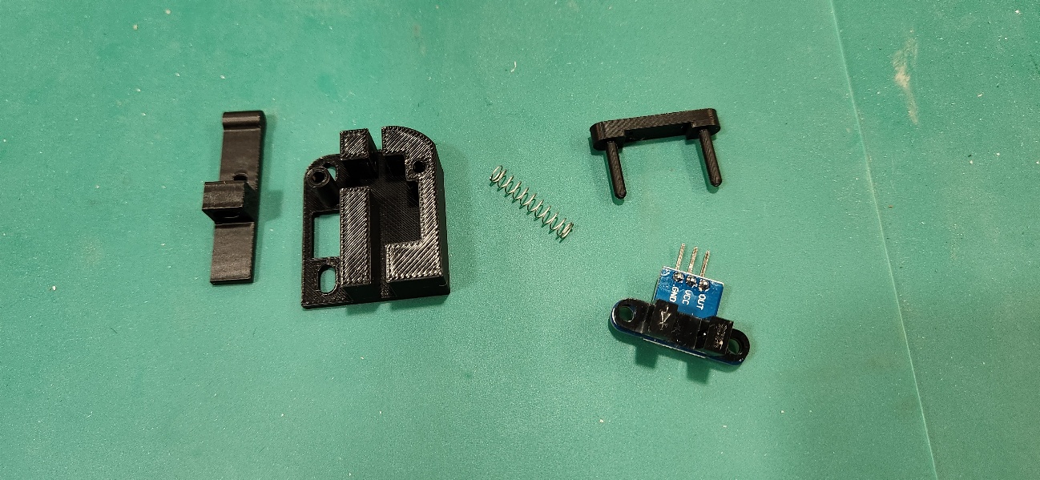
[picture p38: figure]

The optical homing sensor for CS7.2 has been greatly improved and simplified.

The following parts are what is needed for assembly and are available from the CS7.2 repository at:

https://github.com/sjseth/AI-Case-Sorter-CS7.2/blob/main/Models/Classifier/CS7.2%20Homing%20Sensor.stl

Additional components needed for this build are a spring and optical sensor.

- 304 Stainless .3 x 4 x 20mm Compression Spring amazon at: https://www.amazon.com/Cilky-Compressed-Stainless-Diameter-Compression/dp/B0CVRZCPCM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
- IR Sensor Module

https://www.amazon.com/EC-Buying-Optocoupler-Measuring-Interrupter/dp/B0CHDRF497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

## 3D Printing Recommendations

Layer Height: 0.16
Walls: 3
Color: Piston should be black (other colors may not interrupt properly
Infill: 20%

## Assembly Steps

1. Insert spring into piston spring retention hole and hold in place with finger.
2. Insert piston and spring into homing sensor body guiding spring into retention hole in the body  It should look like this when completed.

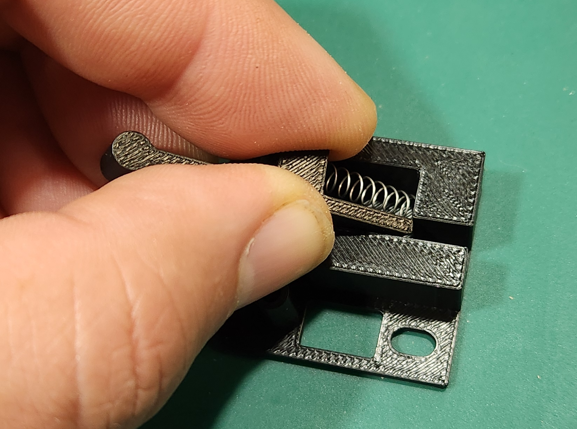
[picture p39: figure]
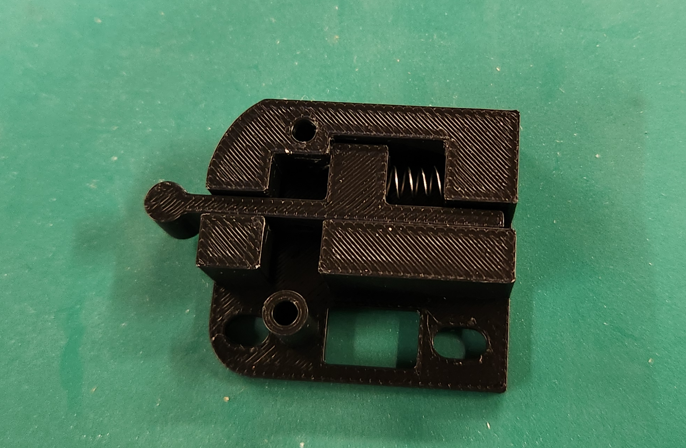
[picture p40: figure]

3. Slide sensor into place and seat all the way against the body of the part.

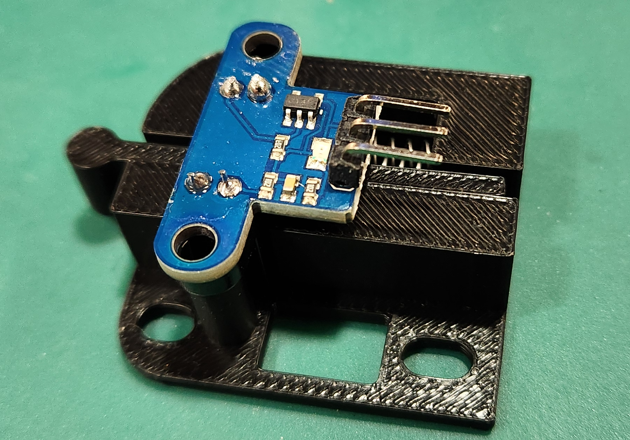
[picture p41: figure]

4. Guide retention clip through sensor mount holes and press firmly to seat against the body of the sensor.

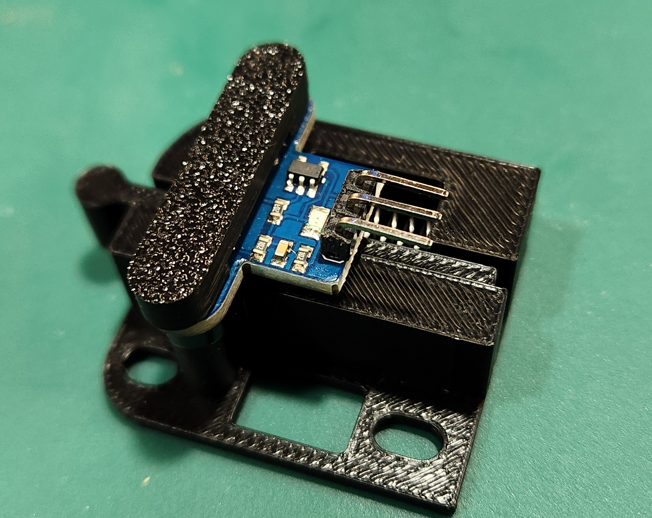
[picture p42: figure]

5. When you attach the wire, it should be connected in the following wire pattern where (Black) Ground is on the left, (Red) 5v+ is center and (Signal) white is on the right

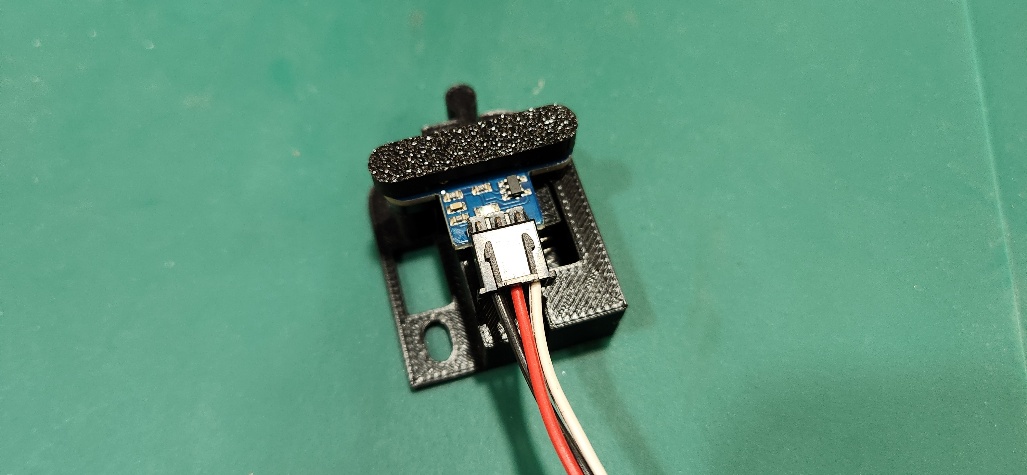
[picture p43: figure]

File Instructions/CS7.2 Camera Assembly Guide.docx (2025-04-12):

# CS7.2 Camera Assembly Guide

# Printing the parts

The models for the 3d printed parts for the camera are available in the “Camera” folder in the GitHub CS7.2 repo.

https://github.com/sjseth/AI-Case-Sorter-CS7.2/tree/main/Models/Camera

From this folder, you need to print both the housing and light diffuser models.

- CS7.2 Camera Housing
- CS7.2 Camera Light Diffuser

The camera housing should be printed using a non-brittle filament such as PLA+ and needs to be black in color.

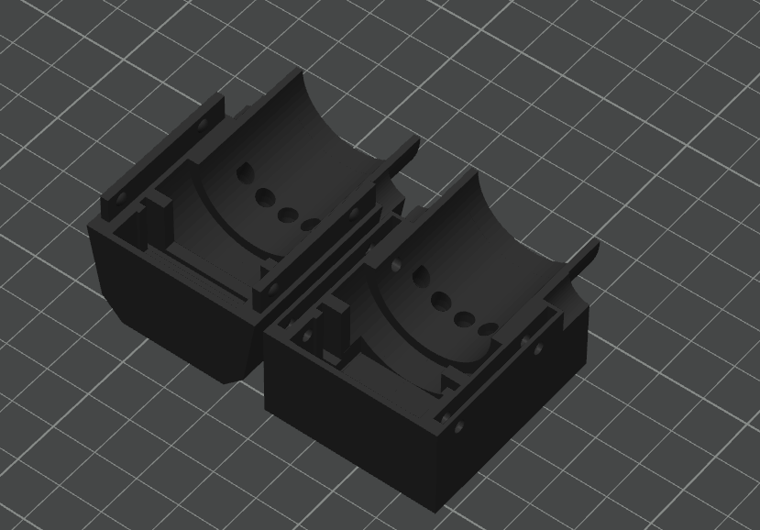
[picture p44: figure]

## Recommended settings for Camera Housing:

Layer height: .2 or finer (.16 recommended)
Filament: PLA+
Color: Black
Supports: Touching build plate
Support Angle: 3 degrees (Bambu/Orca) (or 87 degrees for Cura)
Infill: 15%
Walls: 3
Orientation: see image →

## Settings for Light Diffuser:

Layer height: .2 or finer (.16 recommended)
Filament: Jayo PLA+ (or other non-opaque white filament)
Color: White
Supports: None
Infill: 0 (no infill is very important for this model)
Walls: 2

# Light Ring Assembly.

Depending on how the light ring was purchase, there may be additional assembly required here. If your light ring is already assembled, you can skip this section.

The light ring needs to have a 26AWG wire soldered to it with a length of approximately 60cm or 2ft.

The ring has two solder points labeled plus “+” and minus “-“ where plus is the positive current from your dimmer (typically red or yellow wire) and minus is the ground connector (typically black wire).

1. Strip approximately 8mm of shield from the 26AWG wire pair (recommend red/black pair)
2. Twist the stripped ends to avoid fraying.
3. Feed the wires through the appropriate holes bottom of the light ring and solder at the top (the top is the side with the lights on it)

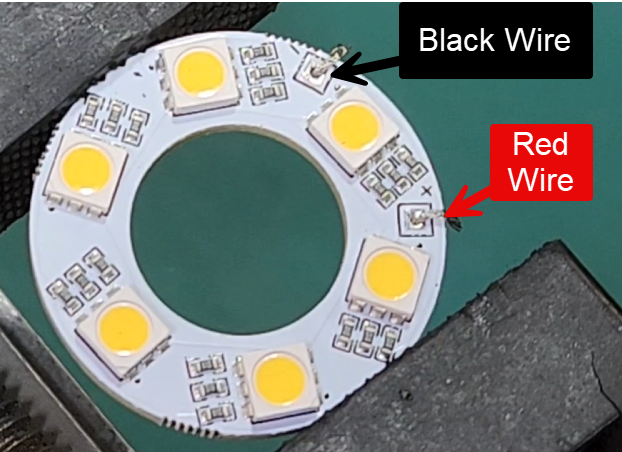
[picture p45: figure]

4. After soldering, clip any excess wire so that the diffuser will sit flat.

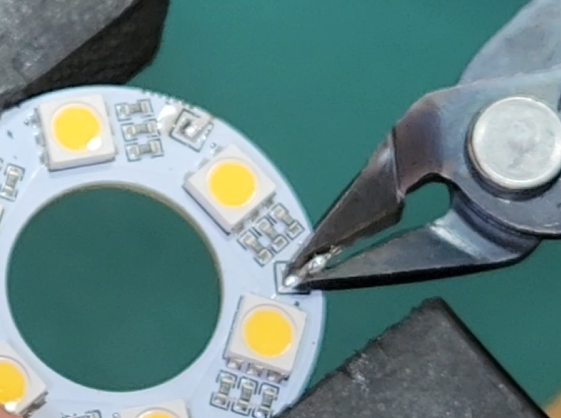
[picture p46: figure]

5. (Optional) Hot glue the diffuser to the light ring. This can easily be done by adding a small amount of hot glue in between one of the lights and pressing and holding the diffuser ring until the glue dries.

# Camera Assembly Steps

1. Locate the camera housing part which has a hole in the side for wiring. Pass both the wire for the usb connector and the light ring through the whole as seen in the picture below:

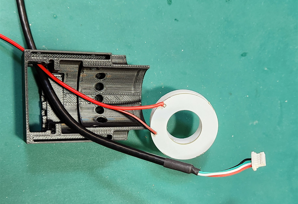
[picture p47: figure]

2. Connect the 5pin mini connector to the camera nd place the light ring over the camera lense.

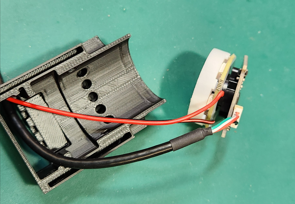
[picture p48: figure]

3. Slide the camera and light ring together down into the slots in the camera housing being sure not to pinch wires or touch the camera lense. The orientation of the wiring should be facing down towards the fan inlet slot.

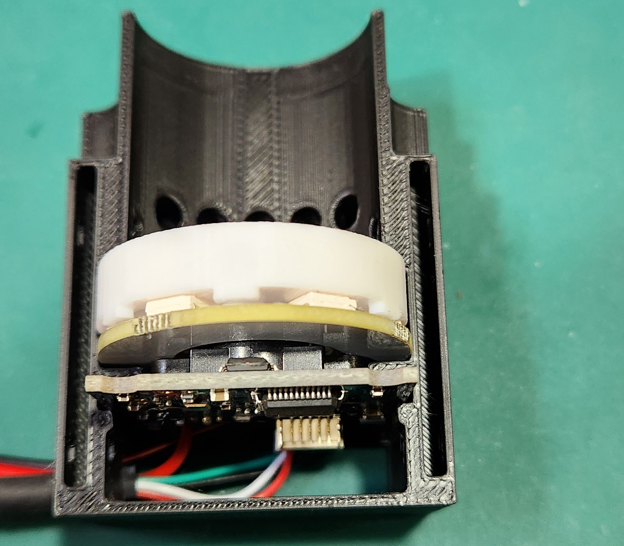
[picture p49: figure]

4. Carefully attach the top housing being sure that all slots are aligned and press fit firmly together until the clamshell parts snap in place.
5. Attach the blower fan so that the air guy (tuyer) is aligned with the air intake slot. See picture below:

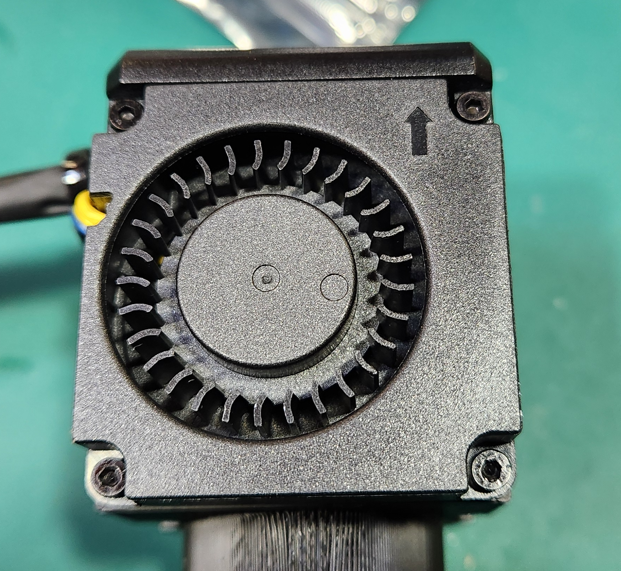
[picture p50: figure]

6. The fan should be attached using two m2x10 and two m2x8 socket head screws. The longer screws are needed on the side which has the air guide.
7. (optional) Use heatshrink tubing or cable organizers to combine the fan and light wires as desired. Use zip ties to connect wires for additional strength.

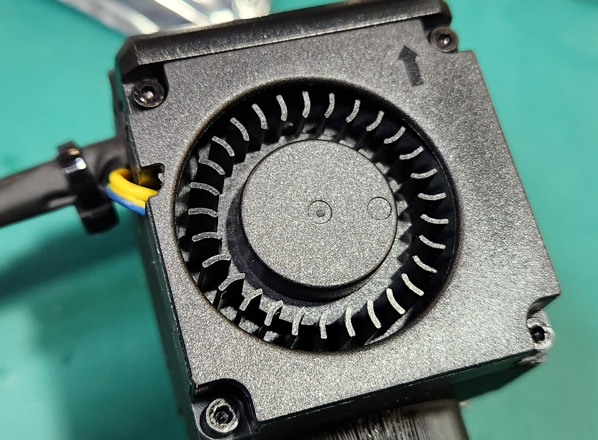
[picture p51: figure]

8. Install ferrules on fan and light ring wire to make it easier to connect to the push terminals on the 7.2 board. The ferrule size needed for 24-26AWG wiring is E0308.

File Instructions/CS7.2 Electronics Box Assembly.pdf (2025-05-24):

# CS7.2 Electronics Enclosure Assembly Guide

## Printing the parts

The models for the 3d printed parts for the classifier base are available in the “Electronics Enclosure” folder in the GitHub CS7.2 repo. https://github.com/sjseth/AI-Case-Sorter-CS7.2/tree/main/Models/Electronics%20Enclosure
From this folder, you need to print the following models.
- CS7.2 Electronics Box
- CS7.2 Electronics Box Lid
- CS7.2 Wire Cover
- CS7.2 Mount with Rotator – Plate
- CS7.2 Mount with Rotator
For these parts here are the basic recommendations:
Filament: PLA+ or PETG.
Color: These parts can be printed in any color you have available.
Layer Height: .2 or finer
Support: Recommend using tree support for the Electronics box, however, use the support mode you get the best results with on your printer. For Bambu printers, I have found these settings work well:

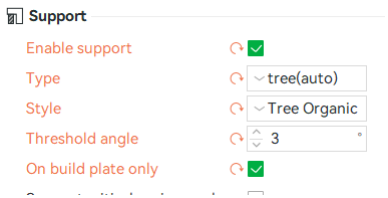
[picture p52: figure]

Note that other slices such as Cura, the support angle may read 87 degrees (opposite of Bambu/Orca slicer)
Strength/Density: 3 walls, 20% infill

## Assembly

Tools Required:

- Screwdriver with bits or Allen keys for M3 socket head cap screws
- Small Phillips head screwdriver
Hardware required:
- (7) M3x5 Phillips Head Screws (Main Board mount)
- (4) M3x14 Phillips Head Counter Sunk (Fan)
- If reversing for intake, use the longer M3x18 countersunk screws
- (4) M3 nuts (Fan Mount)
- (1) M3x8 Phillips Head Screws (box cover lock)
- (1) M3x8 (or longer) Socket Head Screw (Electronics box Mount) Electronics and Misc
- (1) CS7.2 Main Board
- (1) 12v 40mm Fan
- (1) CS7.2 Label Sticker

## Assembly Steps

1. Remove 3d printed support material from Electronics box.
2. Place CS7.2 Main Board into the electronics box aligning the power inputs and switches with the holes. *Important, do not use the motor heatsinks as gripping points as they will come off.
3. Align the riser holes with those on the main board and insert the 7 M3x5 Phillips screws into those hole being sure not to overtighten. Do not put too much downward pressure as if you slip, you can scratch the main board with the screw driver.

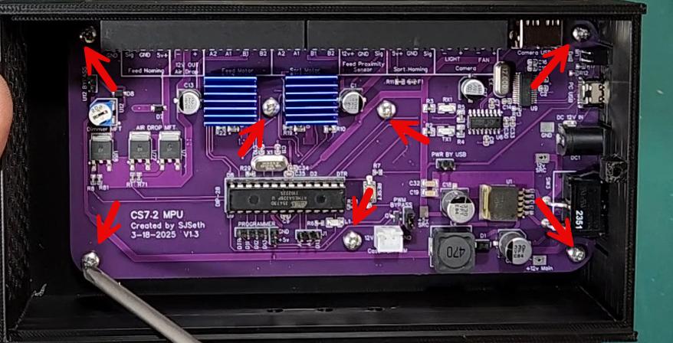
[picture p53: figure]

4. Before installing your fan, ensure that the countersunk recesses are deep enough for your screws to sit even to the top of the lid. If the screws protrude, you may want to use a camfer bit or countersink bit (or even a drill bit) to remove a little more material until the screws are flush.

5. Install fan on to the electronics box lid. The fan should be attached to the “flat side” of the lid meaning the side which does not have countersunk screw holes. Standard orientation is as an exhaust fan which means the M3 nuts will be inserted into the fan nut recesses.

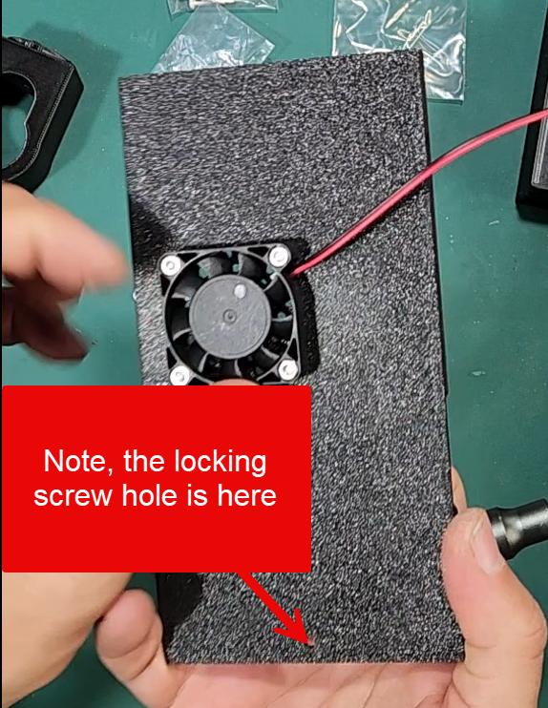
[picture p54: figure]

6. Attach the fan cable to the connector on the main board.

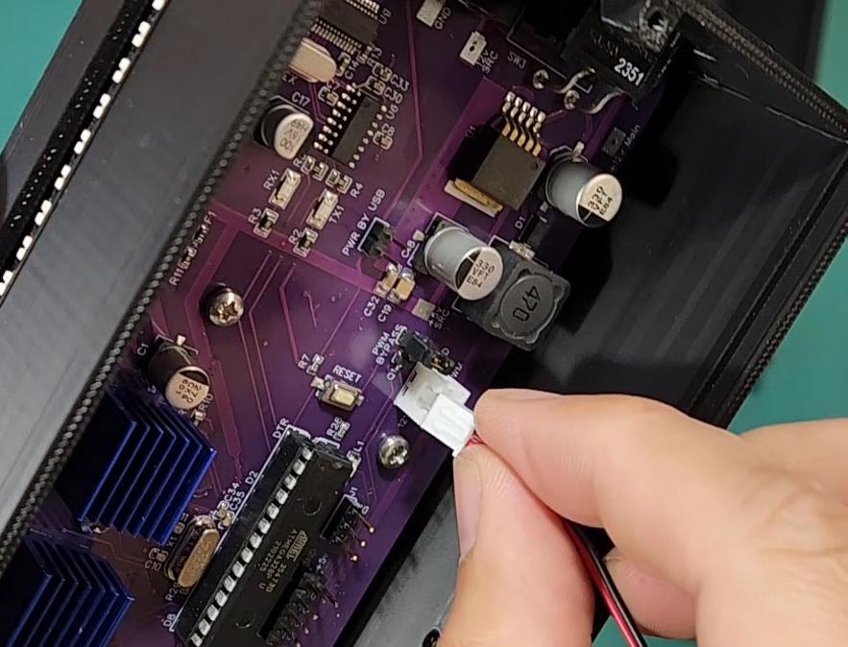
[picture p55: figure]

7. Inspect the electronics box lid to locate the cutout or notch in the rail. Place the opposite rail into the slot so that the fan and wires are inside the box. Align the end of the cutout to the edge of the electronics box and gently press down until the lid sets into the groove. (see example below)

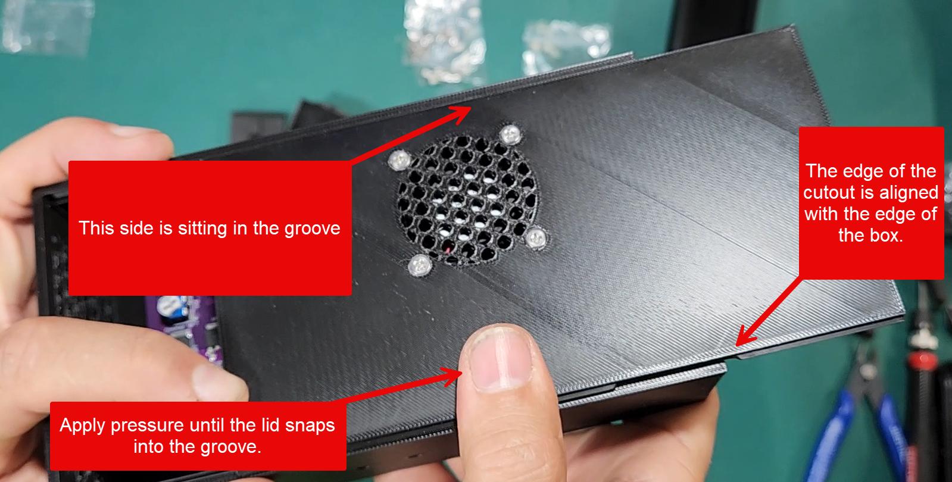
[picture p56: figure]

8. Insert the m3x8 Phillips head counter sunk screw into the lid locking hole near the front end.
9. Peel and place the sticker label into the recess above the spring terminal on the side. Make sure to align the terminals to the sticker.

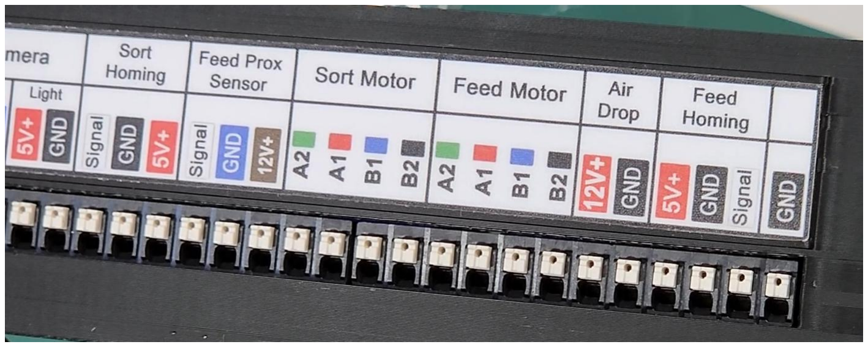
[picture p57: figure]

10. Attach the Mount rotator plate to the mount using an M3x8 or longer socket head screw.
11. The mount can now be attached to the pole when ready using the m6x30 socket screws along with the m6 wingnuts. The box has mount points on the back which slides into the pole mount.

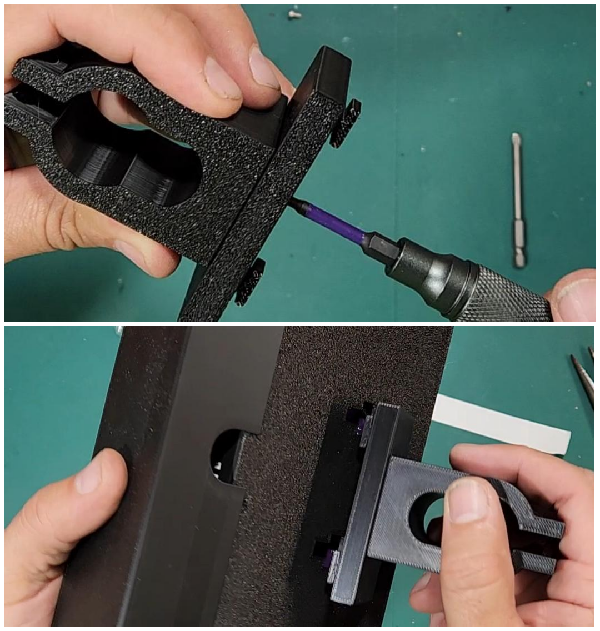
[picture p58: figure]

Lastly the wire cover can be used to provider further wire management once you have connected everything to the electronics board using the spring clamp push terminals. The cover slides over the edge of the box and has holes on the side and end which can be used to route your cables/wires.

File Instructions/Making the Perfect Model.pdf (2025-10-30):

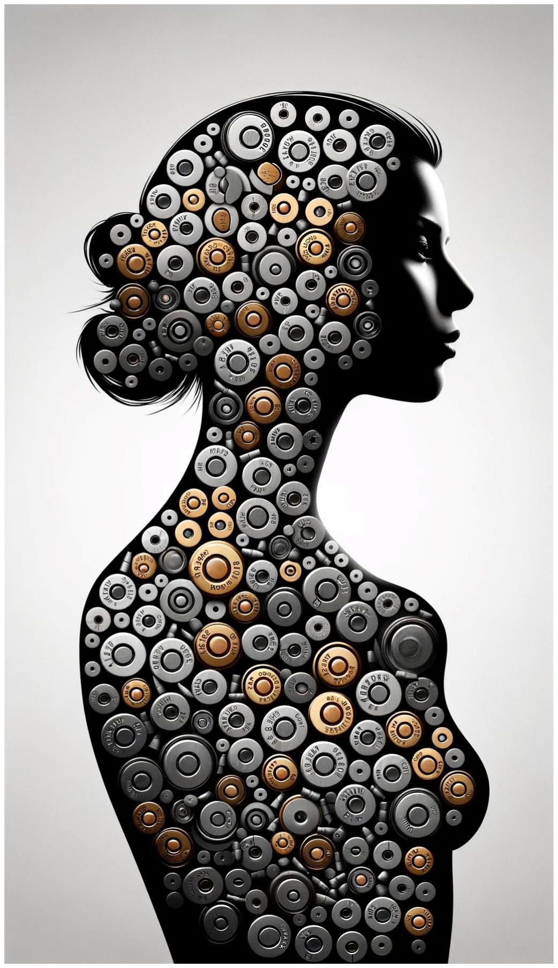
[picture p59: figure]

# Making the Perfect Model

### With AI Headstamp Sorter 1.1.53

# Preparation

When creating a model, it is important to keep “consistency” in mind. This is to say that you want the images you capture to be a near perfect representation of the images that will be captured during the run.
For example, if you are training the model with brass that has been cleaned and shined, you will get best results if you also clean and shine the brass being fed in at run time. As another example, if your light setting is at 50% during training, make sure it is the same at run time. Small changes to the setup between training and runtime can have an impact on accuracy of classification.

# Process Overview

Here is a brief summary of the steps needed to create a flexible and accurate model.
- Create a base model (using proper settings)
- Capture Training Images and define classifications
- Clone and enhance the model.
- Train the cloned model

# Creating a “base”Model

First let’s define a base model. It is a model which you will use as a base to build your run models. The base model will typically be using the standard color mode and leverage primer masking (unless your model is targeted to primers). The base model will typically have 10 – 20+ images per headstamp/classification. Each image will be unique and rotations will not be used here.
Lets go through the steps of setting up the model.
1. On the Models tab, click on the “New” button under the “Create Model” heading.


2. In the create model form, name your model, set processing mode to Color, enable Hide Primer and set mask size to 130. Also ensure Use Deep Learning is selected. (see screenshot)


3. After clicking the Create button, head back over to the Configuration screen and make sure the Enable Image Processing checkbox is checked. Set the Rotations to 1.


4. Next click on the Fine Tuning link to access the capture tuning screen
5. Click the Feed One button until the system has fed a piece of brass over the camera. An image capture should be present in the screen.


You will need to “tune” the settings so that your images are being capture optimally.
- Set the Detection Mode to “Hybrid”
- Click on the center of the primer or primer pocket on the image on the left. This will set the center of your detection area
- Increase or reduce Radius setting until the detection area is just slightly larger than the captured headstamp. The reason it needs to be larger is that not every piece of brass will feed to the same position so you need a buffer around it to ensure that every image will be captured correctly.
- Set Crop Padding to 1. An optimal capture will look like the image on the right in the screenshot above where the arrows show little to no “padding” and the headstamp extends to the edges of the image.
- Set Scan Precision and Scan Sensitivity to 1. This should give you the best capture. You can then increase these values until your captures begin to degrade (off centered). Once you get to that point, you can reduce the value a bit and then use the Feed button to feed 15-20 pieces through the machine to make sure all images are being captured correctly.
- Note that there is a direct relationship to Scan Precision and the Processing Time. As you increase the value of Scan Precision (making it less precise) you will notice the processing time goes down. Ideally you want the highest value here which gives consistently correct images.
- Be sure to hit the Save Changes button before continuing.

6. Now you are ready to begin capturing images for your base model. Click on the Train button to go to the training screen.

# Training Image Capture

While training, you will capture approximately 10-20 examples of each headstamp. You will see a count present in the matrix on the right side of the screen. Once a headstamp gets to 20, you can the Feed button to skip adding additional images for that headstamp and focus on adding more training data for the other headstamps. Continue this process until you have a balanced set of data or run out of brass to capture.

# Classification/Headstamp Creation

You will typically have more success if you avoid “bucket” classifications. For example rather than create a classification for “Federal”, you might consider creating specific classifications such as “FC01”, “FC07”, “Federal-14”, “Federal +P” where the classification corresponds to what is seen on the headstamp. If you wish to sort these all to the same bucket, you can still do that later by selecting all the Federal headstamp variations for a particular slot.

# Clone and Enhance

Once your base model has a sufficient amount of data, we will head back to the Models screen and launch the model enhancer.
Here we are going to clone the base model to a new model and generate rotations as well as balance the model and apply additional image processing (GSBLUR)


If your original base model was set up correctly as indicated earlier in this guide, you will not need to select the Center Images or Add Primer Masks options as those are already included in the base model. The above screenshot has the current recommendations for the best recognition.
- Add Rotations with rotation count set to 8 (in testing little benefit was seen beyond 10 rotations)
- Balance Model
- Processing Mode set to GSBlur with Blur Size: 30 and Blur set to 3

Click the Run button to begin the new model creation using your base model as the source.
The Model Enhancer will begin by cloning the model and then start the enhancement operations.


Once this completed, you will have a model which is nearly ready to Run but still requires that you “Train” the model.
First go back to the model screen and make sure you make the newly cloned model active by selecting it.


Now go to the Training screen and click the “Train Model” button.


Once this operation completes, your model will be ready to use in the Run screen

# Running the Model

The Application Guide covers the various options in the Run screen but since the goal here is to get maximum accuracy, I am going to add a few recommendations about your run settings here as well.
The most accuracy will typically be achieved with the following settings:


Increasing Sample Rotations will give even better results. However, the more rotations that are added, the slower the classifications will be.
Regarding the “Mode” setting, both Serial and Parallel will give the same accuracy however Serial will generally work better on less performant machines while Parallel will be much faster when running on good hardware.

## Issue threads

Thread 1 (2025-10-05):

Train Model, app crashes

WimTakao, 2025-10-05:
When starting "Train Model" the animation starts for a few seconds and then the app crashes.
Assigned 6 GB of memory, 4 cores and 30 GB of free diskspace left.
Windows 10 running on a VM in Proxmox.

Any suggestions hot toe prevent the crashes ?

Faulting application name: AICaseSorter.exe, version: 1.1.53.0, time stamp: 0xe0036e73
Faulting module name: KERNELBASE.dll, version: 10.0.19041.6280, time stamp: 0x56511854
Exception code: 0xe0434352
Fault offset: 0x0000000000025369
Faulting process ID: 0x14f8
Faulting application start time: 0x01dc36042ac58057
Faulting application path: C:\Program Files\SJSeth\AI Brass Sorter\AICaseSorter.exe
Faulting module path: C:\Windows\System32\KERNELBASE.dll
Report ID: 32ec3e60-f993-4ce5-a138-628bcd236e13
Faulting package full name:
Faulting package-relative application ID:

Application: AICaseSorter.exe
Framework Version: v4.0.30319
Description: The process was terminated due to an unhandled exception.
Exception Info: System.DllNotFoundException
   at Tensorflow.c_api.TF_NewGraph()
   at Tensorflow.Graph..ctor()
   at Microsoft.ML.TensorFlow.TensorFlowUtils.LoadTFSessionByModelFilePath(Microsoft.ML.Runtime.IExceptionContext, System.String, Boolean)

Exception Info: System.FormatException
   at Microsoft.ML.TensorFlow.TensorFlowUtils.LoadTFSessionByModelFilePath(Microsoft.ML.Runtime.IExceptionContext, System.String, Boolean)
   at SJSeth.CaseSorter.SJS_MachineLearning.TrainPipelineINCEPTION(Microsoft.ML.MLContext, Microsoft.ML.IDataView)
   at SJSeth.CaseSorter.SJS_MachineLearning.TrainModel(System.Collections.Generic.List`1<SJSeth.CaseSorter.HeadStampData>)
   at System.Threading.ExecutionContext.RunInternal(System.Threading.ExecutionContext, System.Threading.ContextCallback, System.Object, Boolean)
   at System.Threading.ExecutionContext.Run(System.Threading.ExecutionContext, System.Threading.ContextCallback, System.Object, Boolean)
   at System.Threading.ExecutionContext.Run(System.Threading.ExecutionContext, System.Threading.ContextCallback, System.Object)
   at System.Threading.ThreadHelper.ThreadStart()

sjseth, 2025-10-06:
This issue is generally caused by lack of internet connection on first training. Tensorflow needs to download libraries to perform the training.

-------- Original message --------
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

Closed 2025-10-06.

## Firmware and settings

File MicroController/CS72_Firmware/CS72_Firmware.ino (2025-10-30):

/// VERSION CS 7.2.250925.6.1 ///
/// REQUIRES AI SORTER SOFTWARE VERSION 1.1.53 or newer

#include <Wire.h>

//You may need to add the TMCStepper library to your Arduino IDE.
//In the Sketch menu, select Include Library -> Manage Libraries
//In the library manager search for "TMCStepper". Find the TMCStepper library by teemuatlut and click the Install button. 
//You may have to close and reopen the Arduino IDE before the library is recognized
//at this time of this firmware version we are using TMCStepper 0.7.3.
#include <TMCStepper.h>
#include <SoftwareSerial.h>   

#define FIRMWARE_VERSION "7.2.250925.6.1"

#define CASEFAN_PWM 9 //controls case fan speed
#define CASEFAN_LEVEL 100 //0-100 
#define CASEFAN_SW_CTRL false //whether speed controls show in the software

#define CAMERA_LED_PWM 11 //the output pin for the digital PWM 
#define CAMERA_LED_LEVEL  200 //camera brightness if using digital PWM, otherwise ignored 

#define FEED_SENSOR 10 //the proximity sensor under the feed wheel
#define FEED_DIRPIN 8 //DIRECTION signal for the feed motor direction
#define FEED_STEPPIN 7 //PULSE signal for the feed motor steps
#define FEED_ENABLE A0 //Feed motor enable controll pin

//UART COMMS
#define FEED_UART_RX A4 //FEED UART RX COMMS 
#define FEED_UART_TX A5 //FEED UART TX COMMS 
#define FEED_IN_REVERSE false //set to true to reverse direction of feed motor. 
#define FEED_MICROSTEPS 16  //how many microsteps the controller is configured for. 
#define FEED_HOMING_SENSOR A3  //connects to the feed wheel homing sensor
#define FEED_HOMING_SENSOR_TYPE 0 //1=NO (normally open) default switch, 0=NC (normally closed) (optical switches) 
#define FEEDSENSOR_ENABLED true //enabled if feedsensor is installed and working;//this is a proximity sensor under the feed tube which tells us a case has dropped completely
#define FEEDSENSOR_TYPE 1 // NPN = 0 (default), PNP = 1
#define FEED_HOMING_ENABLED true //enabled feed homing sensor
#define FEED_HOMING_OFFSET_STEPS 5 //additional steps to continue after homing sensor triggered
#define FEED_STEPS 60  //The amount to travel before starting the homing cycle. Should be less than (80 - FEED_HOMING_OFFSET_STEPS)
#define FEED_OVERSTEP_THRESHOLD 140 //if we have gone this many steps without hitting a homing node, something is wrong. Throw an overstep error
#define FEED_DONE_SIGNAL 12   // Writes HIGH Signal When Feed is done. Used for mods like AirDrop

//FEED MOTOR SPEED / ACCELLERATION SETTINGS (DISABLED BY DEFAULT)
#define FEED_MOTOR_SPEED 90 //range of 1-100
#define FEED_ACC_SLOPE 32  //2 steps * 16 MicroStes
#define ACC_FEED_ENABLED false //enabled or disables feed motor accelleration. 


#define SORT_DIRPIN 3 //DIRECTION signal for the sorter motor
#define SORT_STEPPIN 2 //PULSE signal for the sorter motor
#define SORT_UART_RX 5 //SORT UART RX COMMS
#define SORT_UART_TX 6 //SORT UART TX COMMS
#define SORT_ENABLE 4 //SORT motor enable control
#define SORT_IN_REVERSE false //reverse direction of sorter motor
#define SORT_MICROSTEPS 16 //how many microsteps the controller is configured for. 
#define SORT_HOMING_SENSOR A2  //connects to the sorter homing sensor
#define SORT_HOMING_SENSOR_TYPE 0 //1=NO (normally open) default switch, 0=NC (normally closed) (optical switches)
#define SORT_HOMING_ENABLED true //home sorter on startup and 0
#define SORT_HOMING_OFFSET_STEPS 0 //additional steps to continue after homing sensor triggered
#define SORT_MOTOR_SPEED 94 //range of 1-100
//SORT MOTOR SPEED / ACCELLERATION SETTINGS (ENABLED BY DEFAULT)
#define ACC_SORT_ENABLED true // default true
#define ACC_FACTOR 1200 //1200 is default factor
#define SORT_ACC_SLOPE 64 //64 is default - slope this is the number of microsteps to accelerate and deaccellerate in a sort. 

//STEPPER MOTOR UART SETTINGS
#define R_SENSE 0.11f 
#define DRIVER_ADDRESS 0b00 
#define FEED_CURRENT 900 //mA - 1100 is default 1amp. 1100=1.1amp, 900=.9amp, etc
#define SORT_CURRENT 900 //mA - 1000 is default 1.1 amp.

//AIRDROP / 12v signaling
#define AIR_DROP_ENABLED false //enables airdrop

#define AUTO_MOTORSTANDBY_TIMEOUT 0 // 0 = disabled; The time in seconds to wait after no motor movement before putting motors in standby

//ARDUINO CONFIGURATIONS
//number of steps between chutes. With the 8 and 10 slot attachments, 20 is the default. 
//If you have customized sorter output drops, you will need to change this setting to meet your needs. 
//Note there are 200 steps in 1 revolution of the sorter motor. 
#define SORTER_CHUTE_SEPERATION 20 


//FEED DELAY SETTINGS

// Used to send signal to add-ons when feed cycle completes (used by airdrop mod). 
// IF NOT USING MODS, SET TO 0. With Airdrop set to 60-100 (length of the airblast)
#define FEED_CYCLE_COMPLETE_SIGNALTIME 100 

// The amount of time to wait after the feed completes before sending the FEED_CYCLE_COMPLETE SIGNAL
// IF NOT USING MODS, SET TO 0. with Airdrop set to 30-50 which allows the brass to start falling before sending the blast of air. 
#define FEED_CYCLE_COMPLETE_PRESIGNALDELAY 30

// Time in milliseconds to wait before sending "done" response to serialport (allows for everything to stop moving before taking the picture): runs after the feed_cycle_complete signal
// With AirDrop mod enabled, it needs about 20-30MS. If airdrop is not enabled, it should be closer to 50-70. 
// If you are getting blurred pictures, increase this value. 
#define FEED_CYCLE_NOTIFICATION_DELAY 120 

//when airdrop is enabled, this value is used instead of SLOT_DROP_DELAY but does the same thing
//Usually can be 100 or lower, increase value if brass not clearing the tube before it moves to next slot. 
#define FEED_CYCLE_COMPLETE_POSTDELAY 100

// number of MS to wait after feedcycle before moving sort arm.
// Prevents slinging brass. 
// This gives time for the brass to clear the sort tube before moving the sort arm. 
#define SLOT_DROP_DELAY 550

//DEBOUNCE is a feature to counteract case bounce which can occur if the machine runs out of brass and a peice of brass drops a distance from
//from the collator to the feeder. It developes speed and bounces of the prox sensor triggering the sensor and bouncing back up to cause a jam. 
//this seeks to eliminate that by adding a small pause to let the case bounce and settle. 

#define DEBOUNCE_TIMEOUT 300 //default 500. The number of milliseconds without sensor activation (meaning no brass in the feed) required to trigger a debounce pause.

#define DEBOUNCE_PAUSE_TIME 500 //default 500.  Set to 0 to disable. The number of milliseconds to pause to wait for case to settle. 

///END OF USER CONFIGURATIONS ///
///DO NOT EDIT BELOW THIS LINE ///
int cameraLEDLevel = CAMERA_LED_LEVEL; 
int caseFanLevel = CASEFAN_LEVEL;
double fanPercentConversion=0;
int notificationDelay = FEED_CYCLE_NOTIFICATION_DELAY;
bool airDropEnabled = AIR_DROP_ENABLED;
int feedCycleSignalTime = FEED_CYCLE_COMPLETE_SIGNALTIME;
int feedCyclePreDelay = FEED_CYCLE_COMPLETE_PRESIGNALDELAY;
int feedCyclePostDelay = FEED_CYCLE_COMPLETE_POSTDELAY;
int slotDropDelay = SLOT_DROP_DELAY;
int dropDelay =  airDropEnabled ? feedCyclePostDelay : slotDropDelay;
int feedDirection = FEED_IN_REVERSE == false;
long autoMotorStandbyTimeout = AUTO_MOTORSTANDBY_TIMEOUT;

int feedCurrent = FEED_CURRENT;
int sortCurrent = SORT_CURRENT;
bool enableSftCurrCtrl = true;

int feedSpeed = FEED_MOTOR_SPEED; //represents a number between 1-100
int feedSteps = FEED_STEPS;
int feedMotorSpeed = 500;//this is default and calculated at runtime. do not change this value

int sortSpeed = SORT_MOTOR_SPEED; //represents a number between 1-100
int sortSteps = SORTER_CHUTE_SEPERATION;
int sortMotorSpeed = 500;//this is default and calculated at runtime. do not change this value
int homingSteps = 0;

int feedMicroSteps = feedSteps * FEED_MICROSTEPS;

const int feedramp = (ACC_FACTOR + (FEED_MOTOR_SPEED /2)) / FEED_ACC_SLOPE;
const int sortramp = (ACC_FACTOR + (SORT_MOTOR_SPEED /2)) / SORT_ACC_SLOPE;
int feedOverTravelSteps = feedMicroSteps - (FEED_OVERSTEP_THRESHOLD * FEED_MICROSTEPS);
int feedOffsetSteps = FEED_HOMING_OFFSET_STEPS;
int feedHomingOffset = feedOffsetSteps * FEED_MICROSTEPS;

bool FeedScheduled = false;
bool IsFeeding = false;
bool IsFeedHoming = false;
bool IsFeedHomingOffset = false;
bool FeedCycleInProgress = false;
bool FeedCycleComplete = false;
bool IsFeedError = false;

int FeedSteps = feedMicroSteps;
int FeedHomingOffsetSteps = feedHomingOffset;
int feedDelayMS = 150;
int sortDelayMS = 400;

bool forceFeed=false;
String input = "";
int qPos1 = 0;
int qPos2 = 0;
int sortStepsToNextPosition = 0;
int sortStepsToNextPositionTracker=0;
bool SortInProgress = false;
bool SortComplete = false;
bool IsSorting = false;
bool IsSortHoming = false;

int sortOffsetSteps = SORT_HOMING_OFFSET_STEPS;
int sortHomingOffset = sortOffsetSteps * SORT_MICROSTEPS;
bool IsSortHomingOffset = false;
int SortHomingOffsetSteps = sortHomingOffset;
bool sorterIsHomed = false;

int slotDelayCalc = 0;

bool IsTestCycle=false;
bool IsSortTestCycle=false;
unsigned long testCycleInterval=0;
unsigned long testsCompleted=0;
int sortToSlot=0;
unsigned long theTime;
unsigned long timeSinceLastSortMove;
unsigned long timeSinceLastMotorMove;
unsigned long msgResetTimer;

//debounce variables
unsigned long lastTrigger = millis();
int triggerTimeout = DEBOUNCE_TIMEOUT;
int debounceTime= DEBOUNCE_PAUSE_TIME;
bool proxActivated = false;
bool sensorDelay = false;


TMC2209Stepper sortmotorUART(SORT_UART_RX, SORT_UART_TX, R_SENSE, DRIVER_ADDRESS);
TMC2209Stepper feedmotorUART(FEED_UART_RX, FEED_UART_TX, R_SENSE, DRIVER_ADDRESS);

void setup() {
  Serial.begin(9600);
  delay(200);

 
  //enable motor controllers 
  pinMode(FEED_ENABLE, OUTPUT);
  pinMode(SORT_ENABLE, OUTPUT);
  digitalWrite(SORT_ENABLE, LOW);
  digitalWrite(FEED_ENABLE, LOW);


  feedmotorUART.begin();                // Initialize driver
  feedmotorUART.toff(4);                 // Enables driver in software
  sortmotorUART.begin();                // Initialize driver
  sortmotorUART.toff(4);                 // Enables driver in software
  delay(500);

  //feedmotorUART.shaft(true);				
  feedmotorUART.rms_current(FEED_CURRENT);       // Set motor RMS current
  feedmotorUART.microsteps(FEED_MICROSTEPS); 
  feedmotorUART.pwm_autoscale(true);
  feedmotorUART.en_spreadCycle(false);   // false = StealthChop / true = SpreadCycle
  feedmotorUART.ihold(2);

 // feedmotorUART.ihold(4);
  sortmotorUART.rms_current(SORT_CURRENT);       // Set motor RMS current
  sortmotorUART.microsteps(SORT_MICROSTEPS); 
  sortmotorUART.pwm_autoscale(true);    // Needed for stealthChop
  sortmotorUART.en_spreadCycle(false);   // false = StealthChop / true = SpreadCycle
  sortmotorUART.ihold(2);

  setSorterMotorSpeed(SORT_MOTOR_SPEED);
  setFeedMotorSpeed(FEED_MOTOR_SPEED);

  pinMode(FEED_DIRPIN, OUTPUT);
  pinMode(FEED_STEPPIN, OUTPUT);
  pinMode(SORT_DIRPIN, OUTPUT);
  pinMode(SORT_STEPPIN, OUTPUT);

  pinMode(FEED_DONE_SIGNAL, OUTPUT);
  pinMode(FEED_HOMING_SENSOR, INPUT);
  pinMode(SORT_HOMING_SENSOR, INPUT);
  pinMode(FEED_SENSOR, INPUT_PULLUP);

   pinMode(CASEFAN_PWM, OUTPUT);
   pinMode(CAMERA_LED_PWM, OUTPUT);


    adjustCameraLED(cameraLEDLevel);
    adjustFanLevel(caseFanLevel);

  digitalWrite(FEED_DIRPIN, feedDirection);
 
  jogSorter();

  IsFeedHoming=true;
  IsSortHoming=true;
  msgResetTimer = millis();
  
   Serial.print(F("Ready\n"));
}


void loop() {
   checkSerial();
   getProxState();
   runSortMotor();
   onSortComplete();
   scheduleRun();
   checkFeedErrors();
   runFeedMotor();
   homeFeedMotor();
   homeSortMotor();
   serialMessenger();
   onFeedComplete();
   runAux();
   MotorStandByCheck();
}

int FreeMem(){
  extern int __heap_start, *__brkval;
  int v;
  return(int) &v - (__brkval ==0 ? (int) &__heap_start : (int) __brkval);
}

bool commandReady = false;
char endMarker = '\n';
char rc;

void recvWithEndMarker() {
    while (Serial.available() > 0 ) {
        rc = Serial.read();
        delay(1);
        if (rc != endMarker) {
            input += rc;
        }
        else {
            commandReady=true; 
            return;
        }
    }
 }
void resetCommand(){
  input="";
  commandReady=false;
}

void checkSerial(){
  if(FeedCycleInProgress==false && SortInProgress==false && Serial.available()>0){
   
      //input = Serial.readStringUntil('\n');
       recvWithEndMarker();
       
       if(!commandReady){
        return;
       }

      if (input.startsWith("stop")) {
         resetCommand();
          FeedScheduled=false;
          IsFeedHoming=false;
          IsFeedHomingOffset = false;
          IsSortHomingOffset = false;
          FeedCycleComplete=true;
          FeedCycleInProgress = false;
          IsTestCycle=false;
        
         // Serial.print(F("ok\n"));
         return;
      } 
      // Serial.print(input);
       
     //this should be most cases
      if (isDigit(input[0])) {
        moveSorterToNextPosition(input.toInt());
        FeedScheduled = true;
        IsFeeding = false;
        scheduleRun();
        resetCommand();
        return;
      }
      if (input.startsWith("homefeeder")) {
        feedDelayMS=400;
          IsFeedHoming=true;
         Serial.print(F("ok\n"));
         resetCommand();
         return;
      } 
      if (input.startsWith("homesorter")) {
        sortDelayMS=400;
           jogSorter();
        qPos1 = 0;
        qPos2 = 0;
          IsSortHoming=true;
          Serial.print(F("ok\n"));
          resetCommand();
         return;
      } 
     if(input.startsWith("status")){
        Serial.print(F("SORT microsteps: "));   Serial.println(sortmotorUART.microsteps());
        Serial.print(F("SORT current: "));   Serial.println(sortmotorUART.rms_current()); 
        Serial.print(F("SORT Stealth: "));   Serial.println(sortmotorUART.stealth()); 
        
        Serial.print(F("FEED microsteps: "));   Serial.println(feedmotorUART.microsteps());
        Serial.print(F("FEED current: "));   Serial.println(feedmotorUART.rms_current()); 
        Serial.print(F("FEED Stealth: "));   Serial.println(feedmotorUART.stealth()); 
        resetCommand();
        return;
     }
      
       if(input.startsWith("feedmotorcurrent:")){
            input.replace("feedmotorcurrent:", "");
            feedCurrent = input.toInt();
            if(feedCurrent>1800){
              feedCurrent=1800;
            }
          feedmotorUART.rms_current(feedCurrent);       // Set motor RMS current
           Serial.print(F("ok\n"));
         resetCommand();
        return;
       }
      if(input.startsWith("sortmotorcurrent:")){
            input.replace("sortmotorcurrent:", "");
            sortCurrent = input.toInt();
            if(sortCurrent>1800){
              sortCurrent=1800;
            }
          sortmotorUART.rms_current(sortCurrent);       // Set motor RMS current
           Serial.print(F("ok\n"));
         resetCommand();
        return;
       }
      if (input.startsWith("sortto:")) {
          input.replace("sortto:", "");
          moveSorterToPosition(input.toInt());
           Serial.print(F("ok\n"));
           resetCommand();
         return;
      } 

      if (input.startsWith("xf:")) {
          input.replace("xf:", "");
          forceFeed = true;
          moveSorterToNextPosition(input.toInt());
          resetCommand();
          FeedScheduled = true;
          IsFeeding = false;
          scheduleRun();
          return;
      }

      if (input.startsWith("getconfig")) {
        Serial.print(F("{\"FeedMotorCurrent\":"));
        Serial.print(feedCurrent);

        Serial.print(F(",\"FeedMotorSpeed\":"));
        Serial.print(feedSpeed);

        Serial.print(F(",\"FeedCycleSteps\":"));
        Serial.print(feedSteps);

        Serial.print(F(",\"SortMotorCurrent\":"));
        Serial.print(sortCurrent);

        Serial.print(F(",\"SortMotorSpeed\":"));
        Serial.print(sortSpeed);

        Serial.print(F(",\"SortSteps\":"));
        Serial.print(sortSteps);

        Serial.print(F(",\"NotificationDelay\":"));
        Serial.print(notificationDelay);

        Serial.print(F(",\"SlotDropDelay\":"));
        Serial.print(slotDropDelay);

        Serial.print(F(",\"AirDropEnabled\":"));
        Serial.print(airDropEnabled);

        Serial.print(F(",\"AirDropPostDelay\":"));
        Serial.print(feedCyclePostDelay);

        Serial.print(F(",\"AirDropPreDelay\":"));
        Serial.print(feedCyclePreDelay);

        Serial.print(F(",\"AirDropSignalTime\":"));
        Serial.print(feedCycleSignalTime);

        Serial.print(F(",\"FeedHomingOffset\":"));
        Serial.print(feedOffsetSteps);

        Serial.print(F(",\"SortHomingOffset\":"));
        Serial.print(sortOffsetSteps);
        
        Serial.print(F(",\"AutoMotorStandbyTimeout\":"));
        Serial.print(autoMotorStandbyTimeout);

        Serial.print(F(",\"CaseFanSpeedEnabled\":"));
        Serial.print(CASEFAN_SW_CTRL);

        Serial.print(F(",\"CaseFanLevel\":"));
        Serial.print(caseFanLevel);

        Serial.print(F(",\"CameraLEDLevel\":"));
        Serial.print(cameraLEDLevel);

        Serial.print(F(",\"DebounceTimeout\":"));
        Serial.print(triggerTimeout);

        Serial.print(F(",\"DebouncePauseTime\":"));
        Serial.print(debounceTime);
  
        Serial.print(F("}\n"));
        resetCommand();
        return;      
      }

        if (input.startsWith("debounceTimeout:")) {
          input.replace("debounceTimeout:", "");
          triggerTimeout = input.toInt();
          Serial.print(F("ok\n"));
          resetCommand();
          return;
        }

        if (input.startsWith("debounceTime:")) {
          input.replace("debounceTime:", "");
          debounceTime = input.toInt();
          Serial.print(F("ok\n"));
          resetCommand();
          return;
        }


       //set feed speed. Values 1-100. Def 60
      if (input.startsWith("feedspeed:")) {
        input.replace("feedspeed:", "");
        feedSpeed = input.toInt();
        setFeedMotorSpeed(feedSpeed);
        Serial.print(F("ok\n"));
        resetCommand();
        return;
      }
      //set feed homing offset
      if (input.startsWith("feedhomingoffset:")) {
        input.replace("feedhomingoffset:", "");
        feedOffsetSteps = input.toInt(); //3
        feedHomingOffset = feedOffsetSteps * FEED_MICROSTEPS; //48
        FeedHomingOffsetSteps = feedHomingOffset; //48

        Serial.print(F("ok\n"));
        resetCommand();
        return;
      }
      if (input.startsWith("sorthomingoffset:")) {
        input.replace("sorthomingoffset:", "");
        sortOffsetSteps = input.toInt(); //3
        sortHomingOffset = sortOffsetSteps * SORT_MICROSTEPS; //48
        SortHomingOffsetSteps = sortHomingOffset; //48

        Serial.print(F("ok\n"));
        resetCommand();
        return;
      }

      if (input.startsWith("sortspeed:")) {
        input.replace("sortspeed:", "");
        sortSpeed = input.toInt();
        setSorterMotorSpeed(sortSpeed);
        Serial.print(F("ok\n"));
        resetCommand();
        return;
      }

      //set sort steps. Values 1-100. Def 20
      if (input.startsWith("sortsteps:")) {
        input.replace("sortsteps:", "");
        sortSteps = input.toInt();
        Serial.print(F("ok\n"));
        resetCommand();
        return;
      }

      //set feed steps. Values 1-1000. Def 100
      if (input.startsWith("feedsteps:")) {
        input.replace("feedsteps:", "");
        feedSteps = input.toInt();
        feedMicroSteps = feedSteps * FEED_MICROSTEPS;
        feedOverTravelSteps = feedMicroSteps - (FEED_OVERSTEP_THRESHOLD * FEED_MICROSTEPS);
        Serial.print(F("ok\n"));
        resetCommand();
        return;
      }
      if (input.startsWith("notificationdelay:")) {
        input.replace("notificationdelay:", "");
        notificationDelay = input.toInt();
        Serial.print(F("ok\n"));
        resetCommand();
        return;
      }
      if (input.startsWith("slotdropdelay:")) {
        input.replace("slotdropdelay:", "");
        slotDropDelay = input.toInt();
        dropDelay =  airDropEnabled ? feedCyclePostDelay: slotDropDelay;
        Serial.print(F("ok\n"));
        resetCommand();
        return;
      }
      if (input.startsWith("airdropenabled:")) {
        input.replace("airdropenabled:", "");
        airDropEnabled = stringToBool(input);
        dropDelay =  airDropEnabled ? feedCyclePostDelay: slotDropDelay;
        Serial.print(F("ok\n"));
        resetCommand();
        return;
      }
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

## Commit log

2025-01-27 updated models
    [CS7.2 Camera Housing.3mf, CS7.2 Camera Housing.stl, CS7.2 Camera Light Diffuser.3mf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]
2025-02-02 added models
    [CS7.1 30.06 Sorter Tube.stl, CS7.1 30.06 Feed Nozzle.stl, CS7.1 30.06 Feed Wheel.stl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]
2025-02-07 added new models
    [CS7.2 Classifier Base.3mf, CS7.2 Classifier Base.stl, CS7.2 Homing Sensor.stl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]
2025-02-07 Update CS7.2 Tension Cam.stl
    [CS7.2 Tension Cam.stl]
2025-02-07 Updated labels
    [CS7.2 Classifier Base.3mf, CS7.2 Pole Mount - 1.050 w-Channel.stl]
2025-02-09 Updated parts
    [CS7.2 - Offset Bracket - BF556 300.stl, CS7.2 Optical Sensor Riser.stl]
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2025-02-11 updated drive gear and brackets
    [CS7.2 Drive Gear.stl, CS7.2 Pipe Bracket wNotch.stl, CS7.2 Pipe Bracket.stl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]
2025-02-11 Update CS7.2 Drive Gear.stl
    [CS7.2 Drive Gear.stl]
2025-02-12 Update CS7.2 Pipe Bracket.stl
    [CS7.2 Pipe Bracket.stl]
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2025-02-13 move offset bracket to mounts
    [CS7.2 - Offset Bracket - BF556 300.stl]
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2025-02-19 Update CS7.2 EB Mount.stl
    [CS7.2 EB Mount.stl]
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2025-02-22 Updates to wire cover
    [CS7.2 EB Wire Cover.3mf, CS7.2 EB Wire Cover.stl]
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2025-02-23 update camera and wire cover
    [CS7.2 Camera Housing.stl, CS7.2 EB Wire Cover.stl]
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2025-02-24 updates homing sensor paths
    [CS7.2 Homing Sensor - 1 unit - JayoPLAPlus.3mf, CS7.2 Homing Sensor - 1 unit - PLA-Generic.3mf, CS7.2 Homing Sensor - 2 units - JayoPLAPLus.3mf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]
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2025-02-27 Create CS7.2 Homing Sensor Kit.stl
    [CS7.2 Homing Sensor Kit.stl]
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2025-03-13 Update CS7.2 Camera Housing.3mf
    [CS7.2 Camera Housing.3mf]
2025-03-22 Create CS7.2 Sort Pipe - 200mm LO.stl
    [CS7.2 Sort Pipe - 200mm LO.stl]
2025-03-23 Update CS7.2 Electronics Box Lid.stl
    [CS7.2 Electronics Box Lid.stl]
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2025-03-23 Update CS7.2 Feed Wheel - 30.06 - (S).stl
    [CS7.2 Feed Wheel - 30.06 - (S).stl]
2025-03-25 Update CS7.2 Feed Wheel - 9mm - 380 (S).stl
    [CS7.2 Feed Wheel - 9mm - 380 (S).stl]
2025-03-26 updated classifier and homing sensors
    [CS7.2 Homing Senso_OpticalV1.stl, CS7.2 Homing Sensor.stl]
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2025-03-26 updated optical homing strategy
    [CS7.2 Optical Sensor Riser.stl, CS7.2 Sorter Base.stl, CS7.2 Sorter Homing Interupt.stl]
2025-03-26 updated cam and brackets
    [CS7.2 Feed Bracket.stl, CS7.2 Tension Cam.stl]
2025-03-27 Update CS7.2 Sorter Base.stl
    [CS7.2 Sorter Base.stl]
2025-03-27 updated base and mounts
    [CS7.2 Classifier Base.stl, CS7.2 Pole Mount - 1.050 w-B_Channel.stl]
2025-03-27 Create CS7.2 Electronics Box - V3.stl
    [CS7.2 Electronics Box - V3.stl]
2025-03-27 updated sorter base, lowered slot
    [CS7.2 Sorter Base.stl]
2025-03-28 Update CS7.2 Electronics Box - V3.stl
    [CS7.2 Electronics Box - V3.stl]
2025-03-28 Update CS7.2 Sorter Homing Interupt.stl
    [CS7.2 Sorter Homing Interupt.stl]
2025-03-30 Update CS7.2 Electronics Box.stl
    [CS7.2 Electronics Box.stl]
2025-04-01 Update CS7.2 EB Wire Cover.stl
    [CS7.2 EB Wire Cover.stl]
2025-04-01 Update CS7.2 EB Wire Cover.3mf
    [CS7.2 EB Wire Cover.3mf]
2025-04-05 Update CS7.2 Pole Mount - 1.050 w-B_Channel.stl
    [CS7.2 Pole Mount - 1.050 w-B_Channel.stl]
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2025-04-16 Update CS7.2 Wheel Lock - Light Shade.stl
    [CS7.2 Wheel Lock - Light Shade.stl]
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2025-04-18 Update CS7.2 Classifier Base.stl
    [CS7.2 Classifier Base.stl]
2025-04-18 updated mount with channel
    [CS7.2 Pole Mount - 1.050 w-B_Channel.stl, CS7.2 Pole Mount - 1.050 with Channel.stl]
2025-04-18 Update CS7.2 Pole Mount - 1.050 with Channel.stl
    [CS7.2 Pole Mount - 1.050 with Channel.stl]
2025-04-19 updated regular mount to add channel
    [CS7.2 Pole Mount - 1.050.stl]
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2025-04-21 Create CS7.2 Wire Mgmt Clip.stl
    [CS7.2 Wire Mgmt Clip.stl]
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2025-04-30 updated readme and base
    [CS7.2 Classifier Base.stl]
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2025-05-24 Updated documentation and organized models
    [CS7.2 EB Mount with Rotator - Plate.stl, CS7.2 EB Mount with Rotator.stl, CS7.2 EB Wire Cover.stl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]
2025-05-30 Added 3d printing instructions matrix
    [3D Printing Instructions.xlsx]
2025-05-31 Updated firmware to fix bug in feed
    [CS72_Firmware.ino]
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2025-06-09 Updated 3d printing instructions
    [3D Printing Instructions.xlsx]
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2025-06-11 fixed spelling on board manual
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2025-06-14 Update CS7.2 Camera Light Diffuser.stl
    [CS7.2 Camera Light Diffuser.stl]
2025-06-19 Update 6.5CM wheel, fixed pipe bracket errors
    [CS7.2 Feed Wheel - 6.5 Creedmoor (S).stl, CS7.2 Pipe Bracket.stl]
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2025-06-21 Added the sorting bins to the repo
    [CS7.2 Sorter Base Mat.stl, CS7.2 Sorter Bin Stackable.stl, CS7.2 Sorter Bin.stl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]
2025-06-26 Update CS7.2 300 Blackout Feed Wheel.stl
    [CS7.2 300 Blackout Feed Wheel.stl]
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2025-07-08 Updated camera housing to add more room for camera components
    [CS7.2 Camera Housing.3mf, CS7.2 Camera Housing.stl]
2025-07-12 Added new CSx Feed Tubes and Drop Nozzles
    [CS7.x 9mm Drop Nozzle.stl, CS7.x 223_556 Feed Tube.stl, CS7.x 30.06 Feed Tube.stl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]
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2025-12-27 Added stallguard support for v1.7 boards
    [CS72_Firmware_V1.7.ino]
2026-01-11 updated feed homing sensor
    [CS7.2 Homing Sensor V2.3mf, CS7.2 Homing Sensor V2.stl, CS7.2 Homing Sensor v1.3mf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]
2026-01-19 Update CS7.2 Homing Sensor V2.stl
    [CS7.2 Homing Sensor V2.stl]
2026-05-23 Create CS7.2 Wire Cover Extended.stl
    [CS7.2 Wire Cover Extended.stl]
2026-05-23 added new tight wheel for 380 and 9mm
    [CS7.x 9mm 380 Feed Wheel - Tight v5.stl, CS7.x Caliber Conversion 6.5cm - 308Win - x39 - most current.3mf]
